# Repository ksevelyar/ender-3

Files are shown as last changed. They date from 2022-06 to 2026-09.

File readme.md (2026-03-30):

# Ender 3
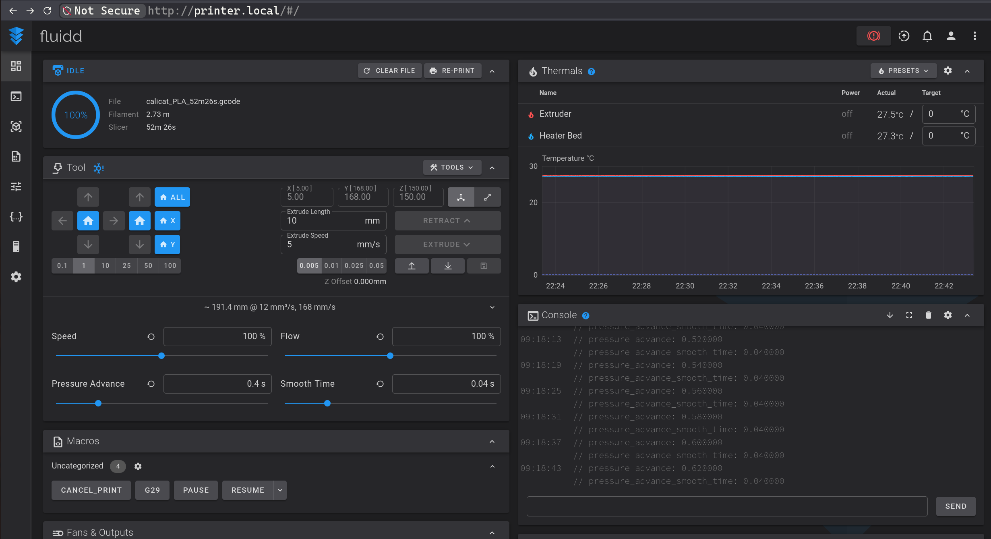
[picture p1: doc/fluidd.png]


## firmware
```
nix build .#klipper-firmware
```

The SKR 1.4 Turbo uses an LPC1769 microcontroller and a Smoothieware-style bootloader. This bootloader only looks for a file named exactly firmware.bin on the root of the microSD card at power-up. If it finds it, it flashes the new firmware and renames the file to FIRMWARE.CUR as proof it worked:

```
cp result/klipper.bin /run/media/ksevelyar/3D-PRINT-0/firmware.bin
```

## sd image
```
nix build .#nixosConfigurations.printer.config.system.build.sdImage --show-trace --impure
```

```
sudo dd if=result/sd-image/nixos-sd-image-24.05.20241230.b134951-armv7l-linux.img of=/dev/sdx bs=4M status=progress oflag=sync
```

## update

```
nixos-rebuild switch --flake .#printer --target-host root@printer.local --no-reexec
```

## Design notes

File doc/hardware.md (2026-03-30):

# Hardware
* [Ender 3 pro](https://github.com/Creality3DPrinting/Ender-3)
* [Banana Pi M2 Zero](https://wiki.banana-pi.org/Banana_Pi_BPI-M2_ZERO)
* SKR 1.4 Turbo + TMC2209
* Auto bed leveling with 3DTouch [[mount]](https://www.thingiverse.com/thing:3003725/files)
* Filament guidance with [filament guide](https://www.thingiverse.com/thing:3052488/files) and [spool roller](https://www.thingiverse.com/thing:3290358/files)
* GT2 timing belt, 6 mm wide, 2 mm pitch

## Assembley
* EXP3 on the LCD to EXP1 on the SKR 1.4
* serial console on pins 8(TxD) and 10(RxD) is mapped to /dev/ttyS3 (UART3) on banana PI M2 Zero

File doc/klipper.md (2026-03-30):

# Klipper
* Ender 3 Pro
* SKR 1.4 Turbo
* TMC2209
* BMG clone
* 3DTouch

## Config refs
* https://github.com/Klipper3d/klipper/blob/master/config/generic-bigtreetech-skr-v1.4.cfg
* https://github.com/Klipper3d/klipper/blob/master/config/printer-creality-ender3pro-2020.cfg

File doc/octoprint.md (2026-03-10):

# Software

* Raspbian
* OctoPrint
* [Bed Visualizer](https://plugins.octoprint.org/plugins/bedlevelvisualizer/)

## Python

tmux new -s py311

mkdir -p ~/python
cd ~/python

wget -O Python-3.11.8.tar.xz https://www.python.org/ftp/python/3.11.8/Python-3.11.8.tar.xz

tar -xf Python-3.11.8.tar.xz
cd Python-3.11.8

./configure
make -j2
sudo make altinstall

/usr/local/bin/python3.11 --version

## OctoPrint

/usr/local/bin/python3.13 -m venv ~/octoprint/venv
~/octoprint/venv/bin/python -m pip install -U pip setuptools wheel

~/octoprint/venv/bin/python -m pip install -U OctoPrint

 ~/octoprint/venv/bin/python -m pip install -U "git+https://github.com/jneilliii/OctoPrint-BedLevelVisualizer.git"

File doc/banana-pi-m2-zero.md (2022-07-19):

# Banana Pi M2 Zero

## Serial

* enable uart3 with `armbian-config`
* connect octoprint to `/dev/ttyS3`

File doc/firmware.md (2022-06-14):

# Firmware

## Configure
* https://www.makenprint.uk/3d-printing/3d-printing-guides/skr-v1-4-marlin-2-setup-part-1/
* https://www.makenprint.uk/3d-printing/3d-printing-guides/skr-v1-4-configuration-h-marlin-2-setup-part-2/

## Generate
* `cd marlin`
* `direnv allow`
* `platformio run`

## Update
* copy `.pio/build/LPC1769/firmware.bin` to an SD card
* plug in the SD card to the printer and power off/on it

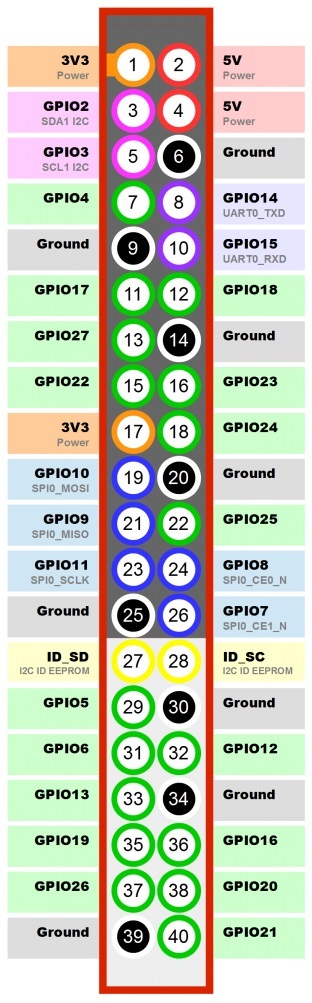
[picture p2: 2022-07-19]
doc/banana-pi-m2-zero-pins.jpg

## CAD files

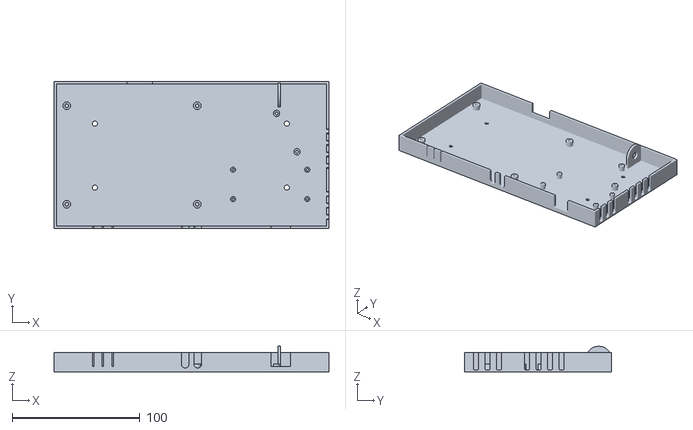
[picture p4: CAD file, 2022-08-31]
case/base.stl
215.0 x 115.0 x 20.0

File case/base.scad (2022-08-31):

$fn=64;
outer_y = 115;
outer_x = 215;
legs_height = 6;
wall_width = 2;
wall_height = 15;
bottom_height = 1.4;

module bottom() {
  module bottom_mounts() {
    translate([32, 32, -0.1]) cylinder(d = 4, h = bottom_height + 1);
    translate([32, 82, -0.1]) cylinder(d = 4, h = bottom_height + 1);

    translate([182, 32, -0.1]) cylinder(d = 4, h = bottom_height + 1);
    translate([182, 82, -0.1]) cylinder(d = 4, h = bottom_height + 1);
  }

  difference() {
    cube([outer_x, outer_y, bottom_height]);
    bottom_mounts();
  }
}

module bpi_m2_zero_mounts() {
  start_x = 140;
  start_y = 23;
  x_dist = 58;
  y_dist = 23;

  module mount() {
    difference() {
      cylinder(d = 4, h = legs_height);
      cylinder(d = 1.9, h = legs_height + 1);
    }
  }

  translate([start_x, start_y, 0]) mount();
  translate([start_x + x_dist, start_y, 0]) mount();
  translate([start_x, start_y + y_dist, 0]) mount();
  translate([start_x + x_dist, start_y + y_dist, 0]) mount();
}

module skr_14t_mounts() {
  x_dist = 102;
  y_dist = 77;
  start_x = 10;
  start_y = (outer_y - y_dist) / 2;

  module mount() {
    difference() {
      cylinder(d = 6, h = legs_height);
      cylinder(d = 3, h = legs_height + 1);
    }
  }

  translate([start_x, start_y, 0]) mount();
  translate([start_x + x_dist, start_y, 0]) mount();
  translate([start_x, start_y + y_dist, 0]) mount();
  translate([start_x + x_dist, start_y + y_dist, 0]) mount();
}

module lm2596_mounts() {
  start_x = 190;
  start_y = 60;
  x_dist = -16;
  y_dist = 30;

  module mount() {
    difference() {
      cylinder(d = 5, h = legs_height);
      cylinder(d = 2.4, h = legs_height + 1);
    }
  }

  translate([start_x, start_y, 0]) mount();
  translate([start_x + x_dist, start_y + y_dist, 0]) mount();
}

module antenna_mount() {
  start_y = outer_y - 20;
  start_x = outer_x - 40;

  module wall() {
    translate([start_x, start_y + 10, 10]) rotate([0, 90, 0]) cylinder(d = 20, h = 2, $fn=64);
    translate([start_x , start_y + 0, 0]) cube([2, 20, 10]);
  }

  module hole() {
    translate([start_x - 0.5, start_y + 10, 10]) rotate([0, 90, 0]) cylinder(d = 6.5, h = 3, $fn=64);
  }

  difference() {
    wall();
    hole();
  }
}

module top_wall() {
  module wall() translate([0, outer_y - wall_width, 0]) cube([outer_x, wall_width, wall_height]);

  module skr_sd_cutout() {
    translate([57, outer_y - 10, legs_height]) cube([20, 20, 100]);
  }

  difference() {
    wall();
    skr_sd_cutout();
  }
}
module bottom_wall() {
  usb_width = 15.2;
  module wall() {
    cube([outer_x, wall_width, wall_height]);
  }

  module usb_cutout() {
    start_x = 198 - 13 - usb_width;
    start_z = 4;
    height = 80;
    translate([start_x, -15, start_z]) cube([usb_width, 30, height]);
  }

  module sleeve_cutout(start_x) {
    width = 6;
    start_z = 6;
    height = 80;

    hull() {
      translate([start_x, 15, start_z]) rotate([90,0,0]) cylinder(d=width,h=30);
      translate([start_x, 15, 80]) rotate([90,0,0]) cylinder(d=width,h=30);
    }
  }

  module ribbon_cutout(start_x) {
    width = 1.2;
    start_z = 4;
    height = 80;
    translate([start_x, -15, start_z]) cube([width, 30, height]);
  }

  difference() {
    wall();
    usb_cutout();

    sleeve_cutout(outer_x / 2 + 5);
    sleeve_cutout(outer_x / 2 - 5);

    ribbon_cutout(30);
    ribbon_cutout(30 + usb_width / 2);
    ribbon_cutout(30 + usb_width);
  }
}
module right_wall() {
  translate([0, 0, 0]) cube([wall_width, outer_y, wall_height]);
}
module left_wall() {
  module wall() {
    translate([outer_x - wall_width, 0, 0]) cube([wall_width, outer_y, wall_height]);
  }

  module avg16_cutout(y) {
    hull() {
      translate([outer_x - 15, y, bottom_height * 2]) rotate([0,90,0]) cylinder(d=4,h=30);
      translate([outer_x - 15, y, 100]) rotate([0,90,0]) cylinder(d=4,h=30);
    }
  }

  difference() {
    wall();
    avg16_cutout(9);
    avg16_cutout(18);
    avg16_cutout(27);

    avg16_cutout(49);
    avg16_cutout(58);
    avg16_cutout(67);
    avg16_cutout(76);
  }
}

bottom();
skr_14t_mounts();
bpi_m2_zero_mounts();
lm2596_mounts();
antenna_mount();

left_wall();
right_wall();
bottom_wall();
top_wall();

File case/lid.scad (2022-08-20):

module socket_cutout() {
  cutout_y = 47.5;
  cutout_x = 27.5;
}

module display_mounts() {
  x_dist = 88;
  y_dist = 64.5;
}

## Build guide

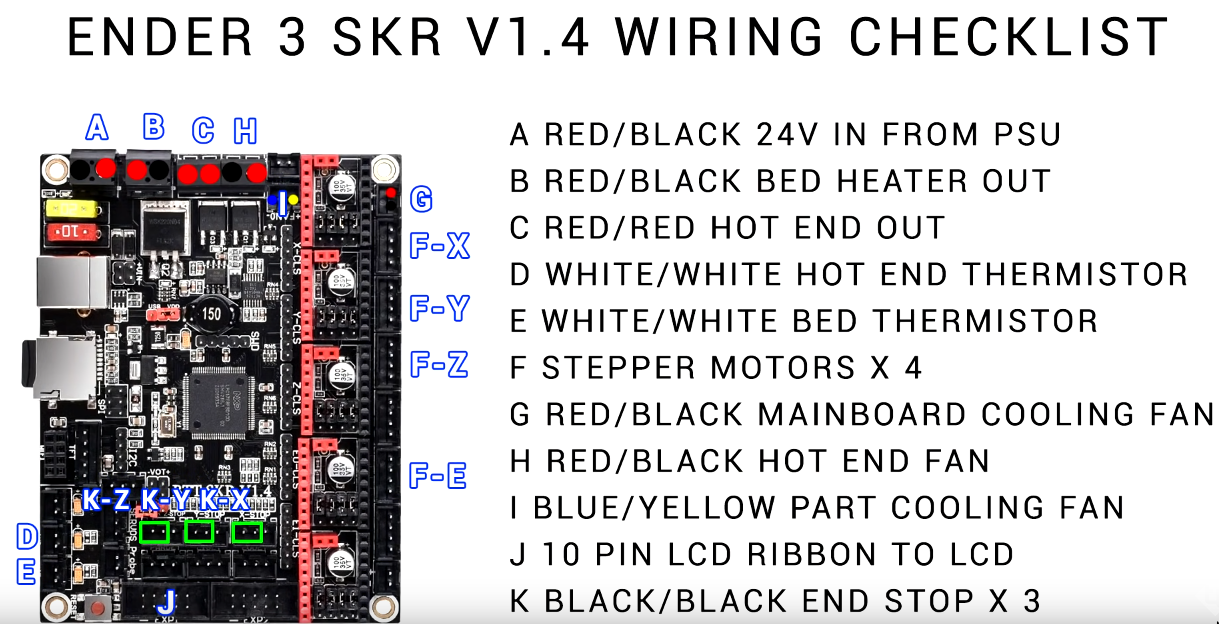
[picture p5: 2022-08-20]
doc/skr-1-4-wiring.png

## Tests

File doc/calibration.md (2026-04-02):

# Printer calibration

## 1. Extruder steps
1) heat hotend to 210C
2) retract 100mm
3) remove bowden

extrude 100mm at 1mm speed, measure delta, adjust extruder.rotation_distance:

```
[extruder]
rotation_distance: 22.939
```

## 2. Check BLTouch
Ensure the BLTouch is mounted vertically and has no wobble.

## 3. Preload silicone spacers
Tighten the bed knobs so the bed is firm.
Silicone spacers should be compressed to ~1/3.

Too tight -> bed corners bend down.
Too loose -> calibration shifts after printing.

## 4. Adjust the bed
Run a 7×7 probe.

Adjust the highest corner, find the highest corner and lower it slightly by tightening the knob.

Repeat probing and adjustment until bed variation is <0.15 mm.

Always lower the highest point (compress spacers).
Do not adjust multiple corners at once.

## PID

```
PID_CALIBRATE HEATER=extruder TARGET=200
```

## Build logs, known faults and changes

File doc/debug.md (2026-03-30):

# Debug

## Device Tree
```
dtc -I dtb -O dts /boot/nixos/5v6534ipxg4rh39p1ip11rgxrg25dkvf-device-tree-overlays/sun8i-h2-plus-bananapi-m2-zero.dtb > current.dts
```

## Serial
```
cat /proc/device-tree/soc/serial@1c28c00/status

okay
```

```
stty -F /dev/ttyS3 -a

speed 0 baud; rows 0; columns 0; line = 0;
intr = ^C; quit = ^\; erase = ^?; kill = ^U; eof = ^D; eol = <undef>; eol2 = <undef>; swtch = <undef>; start = ^Q; stop = ^S; susp = ^Z; rprnt = ^R; werase = ^W; lnext = ^V; discard = ^O; min = 0; time = 0;
-parenb -parodd -cmspar cs8 -hupcl -cstopb cread clocal -crtscts
-ignbrk -brkint -ignpar -parmrk -inpck -istrip -inlcr -igncr -icrnl -ixon -ixoff -iuclc -ixany -imaxbel -iutf8
-opost -olcuc -ocrnl -onlcr -onocr -onlret -ofill -ofdel nl0 cr0 tab0 bs0 vt0 ff0
-isig -icanon -iexten -echo -echoe -echok -echonl -noflsh -xcase -tostop -echoprt -echoctl -echoke -flusho -extproc
```

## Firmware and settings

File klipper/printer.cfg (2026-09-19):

[fan]
pin: P2.3

[heater_fan hotend_fan]
pin: P2.4
heater: extruder
heater_temp: 50.0
fan_speed: 1.0

[mcu]
serial: /dev/ttyS3
baud: 250000
restart_method: command

[bltouch]
sensor_pin: ^P0.10
control_pin: P2.0
x_offset: -37.5
y_offset: -12.5
# NOTE: new nozzle 2.6
z_offset: 2.6
speed: 5

[bed_mesh]
speed: 100
horizontal_move_z: 9
mesh_min: 38, 38
# NOTE: mesh_max_x <= stepper_x.position_max + bltouch.x_offset
# NOTE: Y limited to 210
mesh_max: 192, 192
probe_count: 9,9
algorithm: bicubic

[safe_z_home]
home_xy_position: 155,130
z_hop: 5.0

[printer]
kinematics: cartesian
max_velocity: 300
max_accel: 500
max_z_velocity: 5
max_z_accel: 100

[stepper_x]
step_pin: P2.2
dir_pin: !P2.6
enable_pin: !P2.1
microsteps: 16
rotation_distance: 40
endstop_pin: P1.29
position_endstop: 0
position_max: 230
homing_speed: 25

[tmc2209 stepper_x]
uart_pin: P1.10
interpolate: True
run_current: 0.580
hold_current: 0.290
stealthchop_threshold: 250
diag_pin: ^P1.29
driver_SGTHRS: 53

[stepper_y]
step_pin: P0.19
dir_pin: !P0.20
enable_pin: !P2.8
microsteps: 16
rotation_distance: 40
endstop_pin: P1.28
position_endstop: 0
# FIXME: temporary Y travel limit
position_max: 210
homing_speed: 25

[tmc2209 stepper_y]
uart_pin: P1.9
interpolate: True
run_current: 0.580
hold_current: 0.290
stealthchop_threshold: 250
diag_pin: ^P1.28
driver_SGTHRS: 50

[stepper_z]
step_pin: P0.22
dir_pin: P2.11
enable_pin: !P0.21
microsteps: 16
rotation_distance: 8
endstop_pin: probe:z_virtual_endstop
position_max: 180

[tmc2209 stepper_z]
uart_pin: P1.8
interpolate: True
run_current: 0.580
hold_current: 0.290
stealthchop_threshold: 250

[extruder]
step_pin: P2.13
dir_pin: !P0.11
enable_pin: !P2.12
microsteps: 16
# NOTE: required for e-steps calibration
max_extrude_only_distance: 100
# NOTE: bmg clone
gear_ratio: 50:17
rotation_distance: 22.939

nozzle_diameter: 0.400
filament_diameter: 1.750
heater_pin: P2.7
sensor_type: EPCOS 100K B57560G104F
sensor_pin: P0.24
control: pid
# NOTE: PID_CALIBRATE HEATER=extruder TARGET=220
pid_Kp: 27.149
pid_Ki: 1.724
pid_Kd: 106.9
min_temp: 0
max_temp: 260

[tmc2209 extruder]
uart_pin: P1.4
interpolate: True
run_current: 0.660
hold_current: 0.5

[heater_bed]
heater_pin: P2.5
sensor_type: EPCOS 100K B57560G104F
sensor_pin: P0.25
control: pid
pid_Kp: 54.027
pid_Ki: 0.770
pid_Kd: 948.182
min_temp: 0
max_temp: 130

[display]
lcd_type: st7920
cs_pin: P1.19
sclk_pin: P1.21
sid_pin: P1.23
encoder_pins: ^P1.18, ^P1.20
click_pin: !P0.28

[output_pin beeper]
pin: P1.30
pwm: True
value: 0
shutdown_value: 0

# fix Unknown command:"EXCLUDE_OBJECT_START"
[exclude_object]

# https://docs.fluidd.xyz/configuration/initial_setup
[display_status]
[pause_resume]

[virtual_sdcard]
path: /var/lib/moonraker/gcodes

[gcode_macro PAUSE]
description: Pause the actual running print
rename_existing: PAUSE_BASE
# change this if you need more or less extrusion
variable_extrude: 1.0
gcode:
  ##### read E from pause macro #####
  {% set E = printer["gcode_macro PAUSE"].extrude|float %}
  ##### set park positon for x and y #####
  # default is your max posion from your printer.cfg
  {% set x_park = printer.toolhead.axis_maximum.x|float - 5.0 %}
  {% set y_park = printer.toolhead.axis_maximum.y|float - 5.0 %}
  ##### calculate save lift position #####
  {% set max_z = printer.toolhead.axis_maximum.z|float %}
  {% set act_z = printer.toolhead.position.z|float %}
  {% if act_z < (max_z - 2.0) %}
      {% set z_safe = 2.0 %}
  {% else %}
      {% set z_safe = max_z - act_z %}
  {% endif %}
  ##### end of definitions #####
  PAUSE_BASE
  G91
  {% if printer.extruder.can_extrude|lower == 'true' %}
    G1 E-{E} F2100
  {% else %}
    {action_respond_info("Extruder not hot enough")}
  {% endif %}
  {% if "xyz" in printer.toolhead.homed_axes %}
    G1 Z{z_safe} F900
    G90
    G1 X{x_park} Y{y_park} F6000
  {% else %}
    {action_respond_info("Printer not homed")}
  {% endif %} 

[gcode_macro RESUME]
description: Resume the actual running print
rename_existing: RESUME_BASE
gcode:
  ##### read E from pause macro #####
  {% set E = printer["gcode_macro PAUSE"].extrude|float %}
  #### get VELOCITY parameter if specified ####
  {% if 'VELOCITY' in params|upper %}
    {% set get_params = ('VELOCITY=' + params.VELOCITY)  %}
  {%else %}
    {% set get_params = "" %}
  {% endif %}
  ##### end of definitions #####
  {% if printer.extruder.can_extrude|lower == 'true' %}
    G91
    G1 E{E} F2100
  {% else %}
    {action_respond_info("Extruder not hot enough")}
  {% endif %}  
  RESUME_BASE {get_params}

[gcode_macro CANCEL_PRINT]
description: Cancel the actual running print
rename_existing: CANCEL_PRINT_BASE
gcode:
  TURN_OFF_HEATERS
  CANCEL_PRINT_BASE

[gcode_macro DRY_FILAMENT]
gcode:
  {% set temp = params.TEMP|default(60)|int %}
  {% set hours = params.HOURS|default(6)|int %}
  {% set duration = hours * 3600 %}
  {% set warmup = 600 %}

  SET_IDLE_TIMEOUT TIMEOUT={duration + warmup}
  M140 S{temp}
  UPDATE_DELAYED_GCODE ID=STOP_DRY_FILAMENT DURATION={duration}

[delayed_gcode STOP_DRY_FILAMENT]
gcode:
  M140 S0
  SET_IDLE_TIMEOUT TIMEOUT={printer.configfile.settings.idle_timeout.timeout}

[gcode_shell_command take_android_photo]
command: /run/current-system/sw/bin/adb shell input keyevent 27
timeout: 2
verbose: true

[gcode_macro TAKE_ANDROID_PHOTO]
gcode:
  RUN_SHELL_COMMAND CMD=take_android_photo

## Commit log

2022-05-20 case: module ventilation()
    [power-plug-bracket.scad]
2022-05-20 case: format
    [power-plug-bracket.scad]
2022-05-20 case: add mount_holes() and walls()
    [power-plug-bracket.scad]
2022-05-21 initial version of power-plug-bracket.scad
    [power-plug-bracket.scad]
2022-05-22 add case/base.scad
    [base.scad]
2022-05-24 add mounts for skr 1.4 turbo & bpi m2 zero
    [base.scad]
2022-05-24 add mounts for lm2596
    [base.scad]
2022-06-04 parametric legs height
    [base.scad, base.stl]
2022-06-05 add mounts for display and antenna
    [base.scad, base.stl]
2022-06-10 minimal setup for lm2596 test
    [base.scad, base.stl, power-plug-bracket.scad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]
2022-06-11 adjust measurements
    [base.scad, base.stl, power-plug-bracket.scad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]
2022-06-12 refactor power-plug-bracket.scad
    [power-plug-bracket.scad, power-plug-bracket.stl]
2022-06-14 improve display_mounts()
    [base.scad]
2022-06-14 clean up readme and doc
    [base.scad]
2022-08-20 rotate lm2596 & bpi mounts
    [base.scad]
2022-08-20 add the wiring scheme
2022-08-20 init case walls
    [base.scad, lid.scad, power-plug-bracket.scad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]
2022-08-27 add cutout for usb
    [base.scad]
2022-08-28 add cutouts for the bottom wall
    [base.scad]
2022-08-28 add cutouts for the left wall
    [base.scad]
2022-08-28 refactor cutout functions and positions
    [base.scad, base.stl]
2022-08-31 add access to the sd card of skr
    [base.scad]
2022-08-31 bump stl
    [base.scad, base.stl]
2025-07-20 update marlin to 2.1.2.5, create flake for platformio, enable HOST_ACTION_COMMANDS
    [Configuration.h, Configuration_adv.h, esp32.csv]
2025-12-28 fix value of extruder steps
    [Configuration.h]
2025-12-28 reduce linear advance
    [Configuration.h, Configuration_adv.h]
2026-01-28 replace extruder with bmg; disable speaker; increase bufsize; set 9 points for bltouch
    [Configuration.h, Configuration_adv.h]
2026-03-10 add initial flake for Banana Pi M2 Zero; calibrate e-steps for bmg clone
    [Configuration.h, Configuration_adv.h]
2026-03-11 add doc/calibration.md
    [Configuration.h]
2026-03-17 migrate from octoprint to klipper
    [printer.cfg]
2026-03-22 fix firmware build, fix klipper build, fix agenix build, bake impure ssh key for agenix
    [Configuration.h, Configuration_adv.h, esp32.csv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]
2026-03-22 switch kernel to 6.12.7
2026-03-25 allow connection to fluidd from local network
    [printer.cfg]
2026-03-25 enable UART3 on Banana Pi M2 Zero (ttyS3) for Klipper
2026-03-25 add devShell with klipper-genconf
2026-03-25 rewrite klipper config, add fluidd macros
    [printer.cfg]
2026-03-26 fix bltouch config
    [printer.cfg]
2026-03-26 fix beeper noise
    [printer.cfg]
2026-03-27 add heater_fan
    [printer.cfg]
2026-03-29 fix unknown command EXCLUDE_OBJECT_START
    [printer.cfg]
2026-03-29 adjust bed mesh
    [printer.cfg]
2026-03-30 tune velocity settings
    [printer.cfg]
2026-04-02 add DRY_FILAMENT macro
    [printer.cfg]
2026-04-02 add TAKE_ANDROID_PHOTO macro
    [printer.cfg]
2026-05-03 set explicit logging for klipper
    [printer.cfg]
